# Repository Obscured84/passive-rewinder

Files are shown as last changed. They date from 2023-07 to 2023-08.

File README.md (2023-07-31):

# passive-rewinder
Files in origin_design directory are the untouched files from the creator lenglengda
Passive MMU Rewinder 

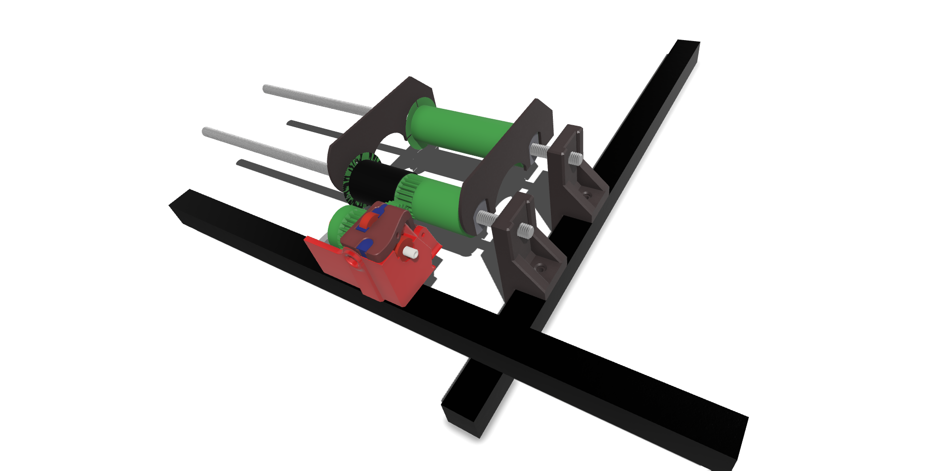
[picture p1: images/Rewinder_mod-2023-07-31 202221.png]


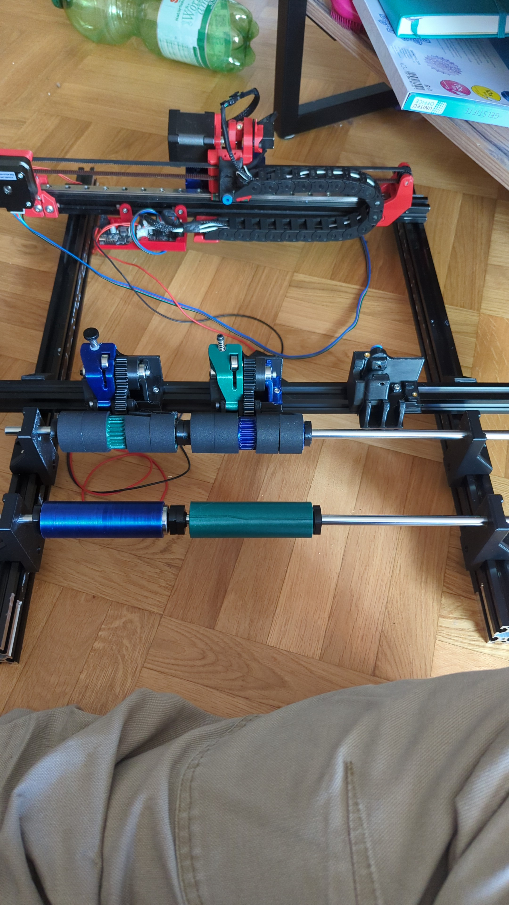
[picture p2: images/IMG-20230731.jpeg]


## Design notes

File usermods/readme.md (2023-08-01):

in case of modifications, please put them in here with your name and proper description

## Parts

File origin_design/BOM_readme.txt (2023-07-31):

BOM:
CSK8PP Clutch Bearing x1
ECAS04 x1
608 Bearing x4
625 Bearing x1
605 Bearing x3
Heat insert M3x4x5 x2
Spring 1x6x10 x1
MK8 or BMG Gear x1
M3 Washer x2
M3x6(8) x1
M3x(10+) x1
M3x(32+) x2 
M3x(48+) x1
M5x(5+) x4 (FH, Optional)
5x50 D-Shaft x1 (Optional)

Notice:
 
- Do confirm the direction of the cltuch bearing before pressing it in.
- Pad a pulley under the bearing and punch it out if it was pressed in the oppsite way.

- A SH M3x48 screw should be insert into the BMG/MK8 gear as shaft
from the side of CSK8PP. (For M3x48 screw + printed shaft user. No need if using D-shaft)
- (D-shaft is recommended for a smoother rotation)

- Install washer to both ends of the spring.
- The spring should be precompressed to keep filament from slipping.

- This rewinder is designed for 5.8L dry box.

- Install TPU sleeves to the rewinding wheel if it is too slippy.

Change Log:

1.0: First test completed
1.1: Added TPU sleeve (optional)
1.2: Adapted clutch bearing shaft to BMG and MK8 gears. Add MK8 spacer.
1.3: Fixed cracking problem of the base by adding more thickness.
1.4: Fixed pressure lever overhang issue
1.5: Change clutch bearing shaft to tightening assembly for better concentricty.
     Added drilling jig for 5.8L dry box.
1.6: Added D-shaft (optional) for better concentricty.
     Added buckle to the desiccant cap to prevent spilling out.
1.7: Fixed holes for D-shaft.
1.8: Added TPU seal for filament outlet.
2.0: Fixed filament stucking issue.
     Adjusted the hight of the lever for smoother filament change.
2.1:  Fixed the bearing seat mismatch issue.

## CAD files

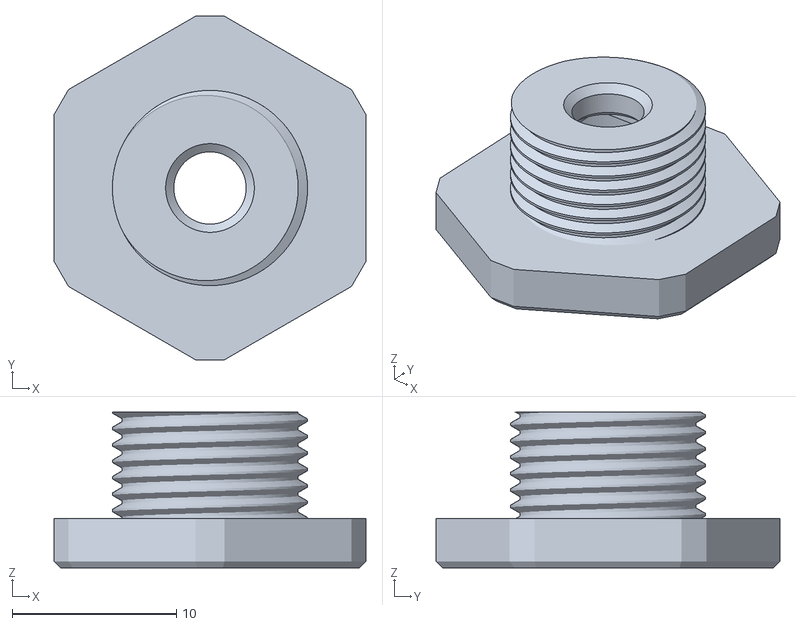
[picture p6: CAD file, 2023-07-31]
origin_design/ECAS_adapter.stl
19.0 x 20.9 x 9.50

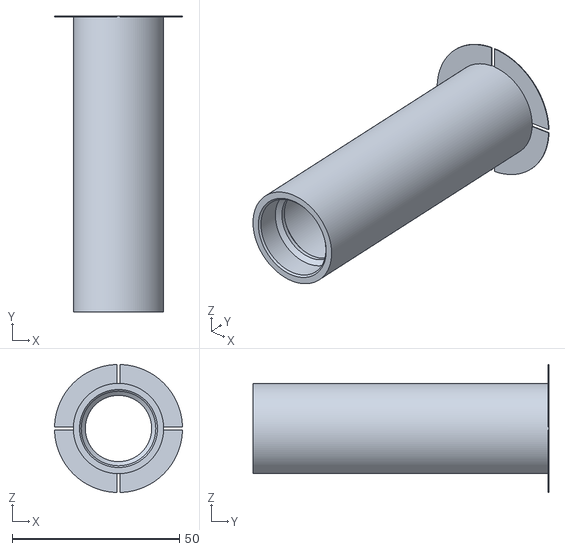
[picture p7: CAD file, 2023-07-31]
STL/Rewinder_mod_rear_spool.stl
38.3 x 88.4 x 38.3

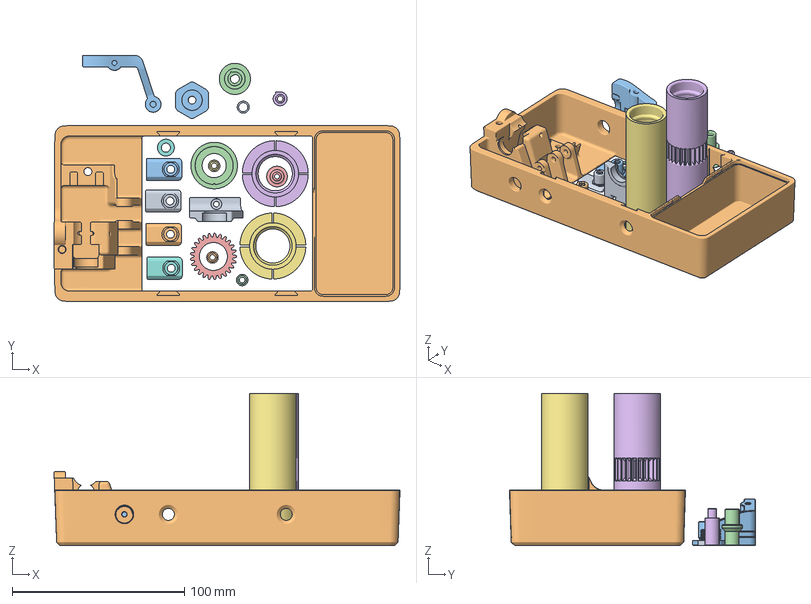
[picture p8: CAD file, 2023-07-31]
origin_design/rewinder.3mf
200.8 x 142.8 x 88.4 mm
bearing_seat.stl
base.stl
lever.stl
clutch_bearing_shaft_d_shaft.stl
clutch_bearing_shaft_screw_1.stl
clutch_bearing_shaft_screw_2.stl
605_pin.stl
605_spacer.stl
BMG_spacer.stl
625_pinx2.stl x 2
ECAS_adapter.stl
clutch_bearing_gear.stl
countershaft_gear.stl
drive_wheel.stl
driven_wheel.stl
608_pinx4.stl x 4

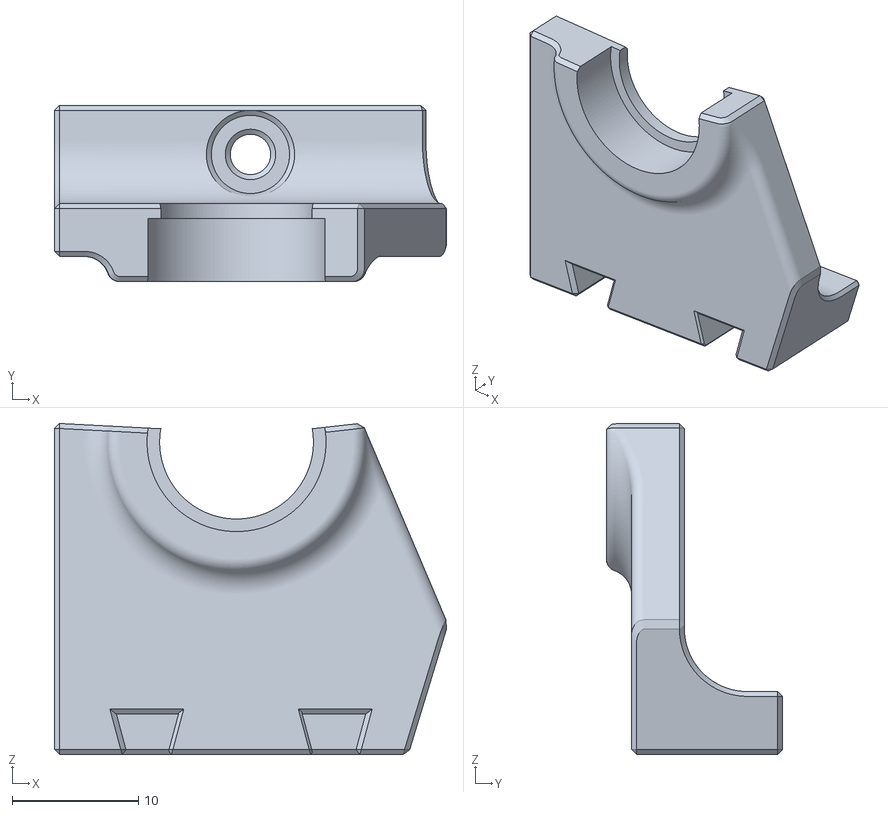
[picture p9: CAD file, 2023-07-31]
STL/Rewinder_mod_bearring_slider.stl
31.1 x 14.0 x 26.3

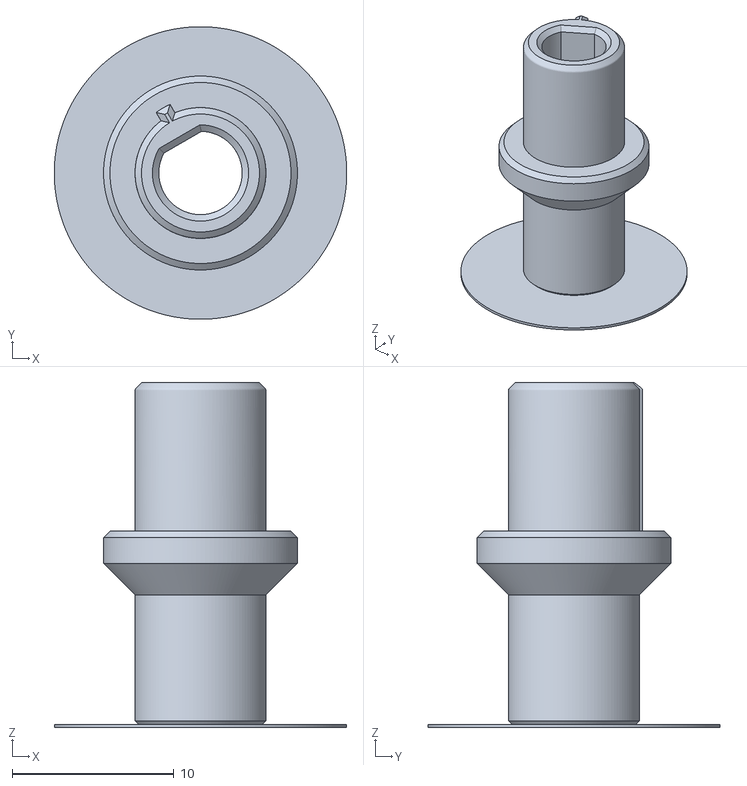
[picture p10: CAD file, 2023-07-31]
origin_design/clutch_bearing_shaft_d_shaft.stl
18.1 x 18.1 x 21.4

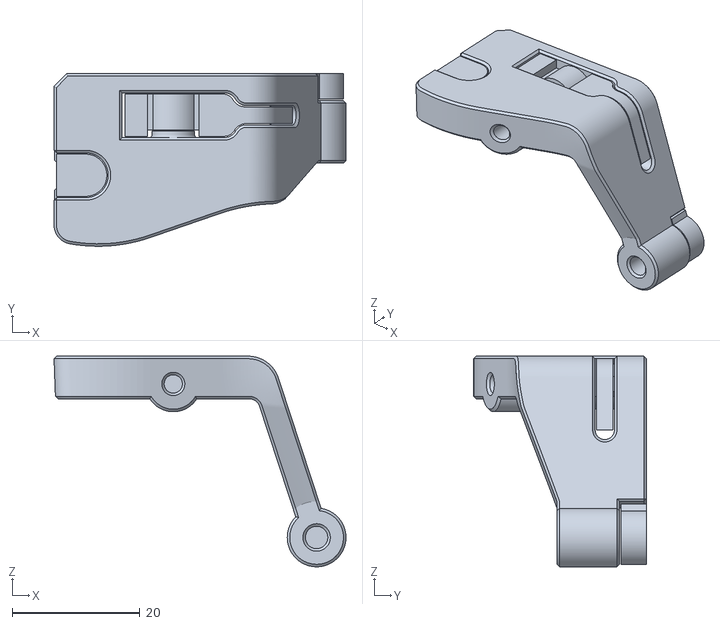
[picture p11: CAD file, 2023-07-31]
STL/Rewinder_mod_lever.stl
45.7 x 27.0 x 33.0

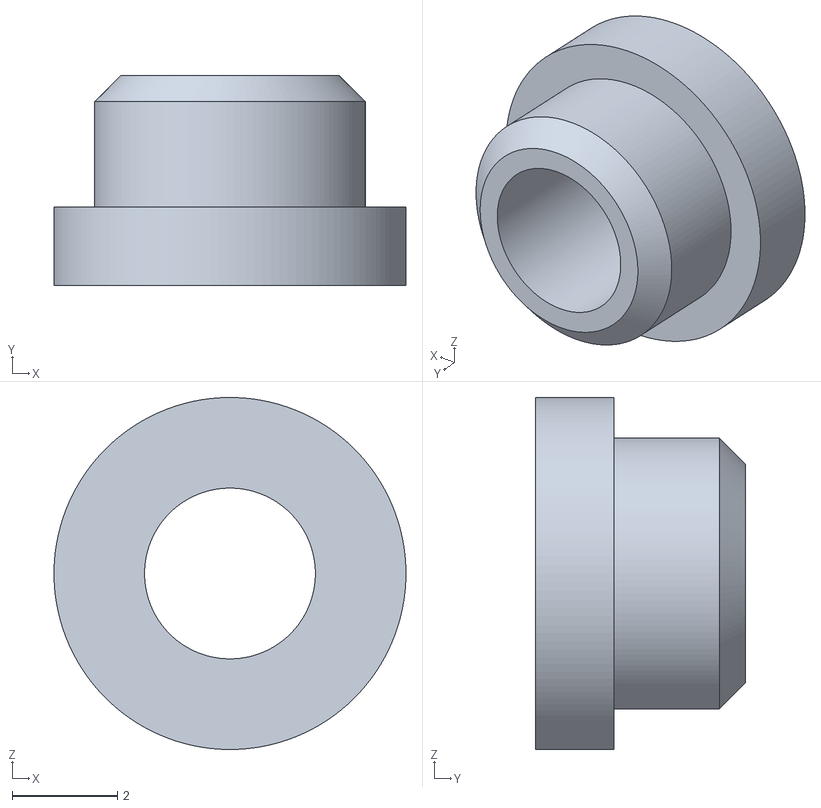
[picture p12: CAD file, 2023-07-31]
STL/Rewinder_mod_625_spacer.stl
6.70 x 4.00 x 6.70

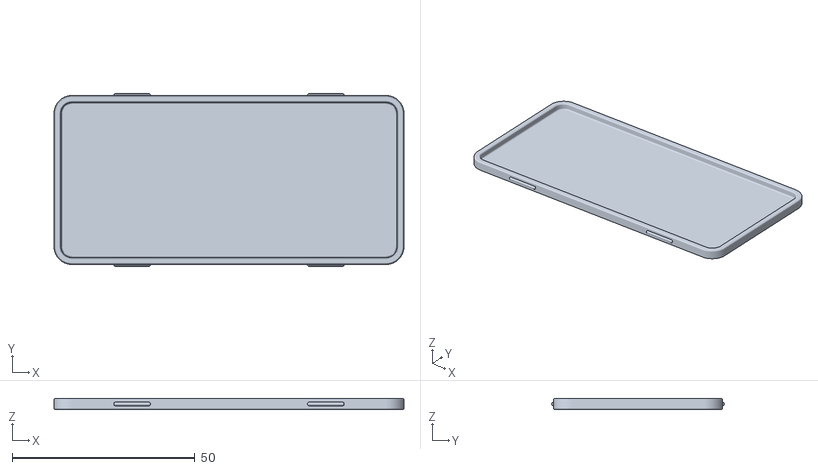
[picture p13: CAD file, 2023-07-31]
origin_design/cap.stl
95.8 x 47.2 x 3.00

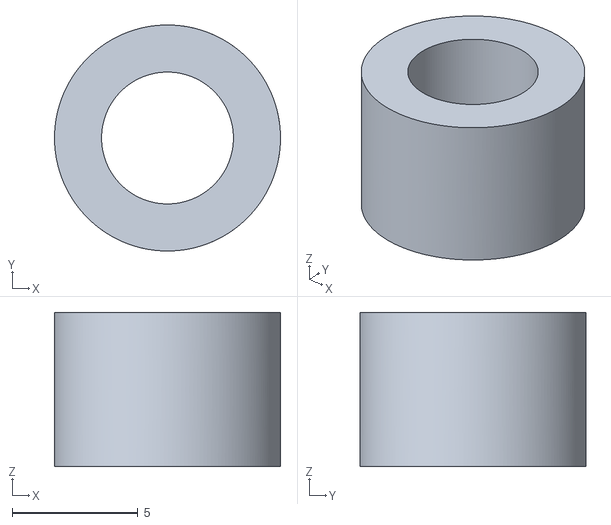
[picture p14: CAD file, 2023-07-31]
origin_design/MK8_spacer.stl
9.00 x 9.00 x 6.15

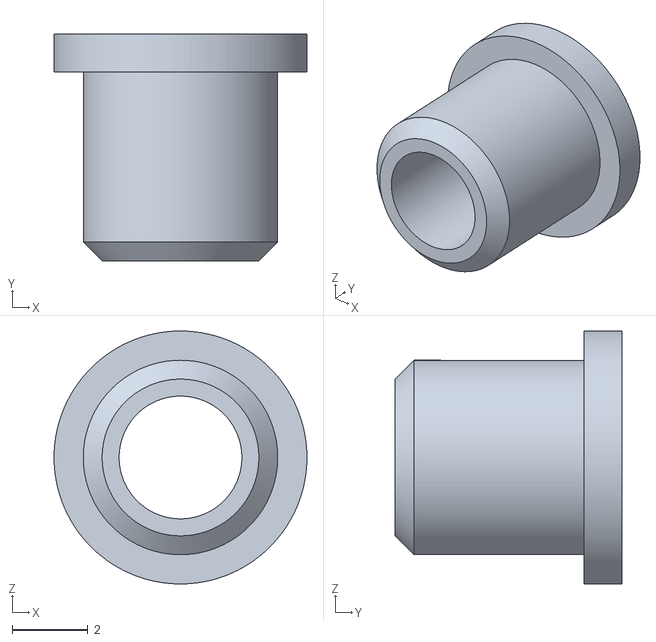
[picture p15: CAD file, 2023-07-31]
STL/Rewinder_mod_605_spacer.stl
6.70 x 6.00 x 6.70

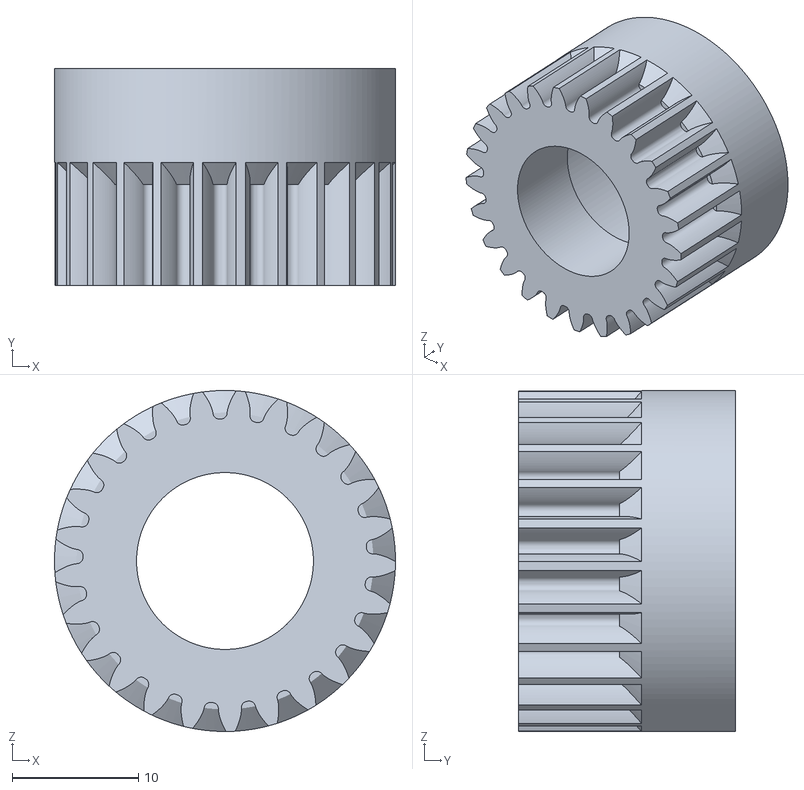
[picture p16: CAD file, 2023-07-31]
STL/Rewinder_mod_clutch_gear.stl
27.0 x 17.2 x 27.0

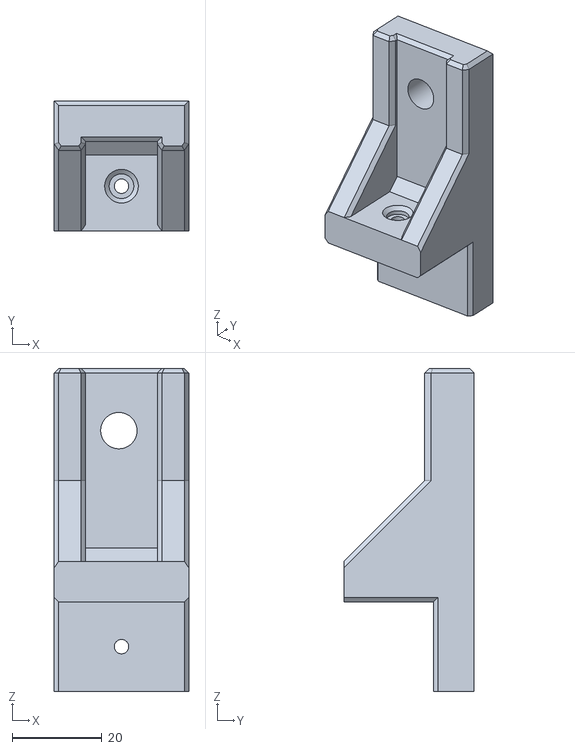
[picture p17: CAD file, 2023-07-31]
STL/Rewinder_mod_spool_anchor4x.stl
30.0 x 29.0 x 72.0

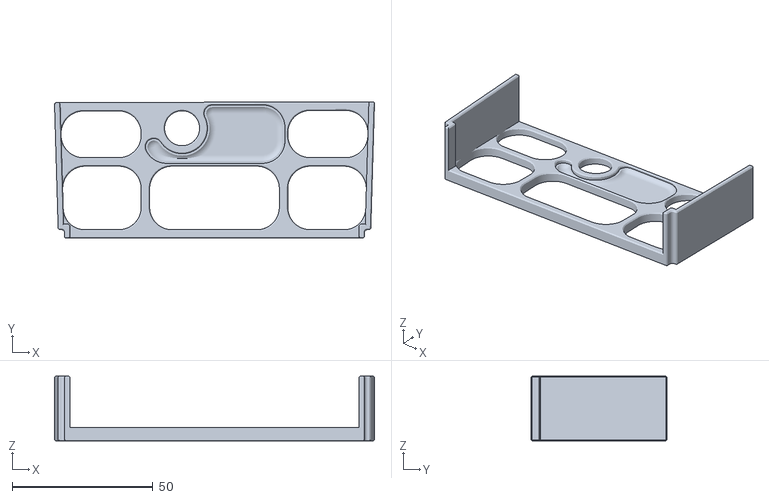
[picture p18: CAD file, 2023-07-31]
origin_design/drilling_jig.stl
113.5 x 48.4 x 23.0

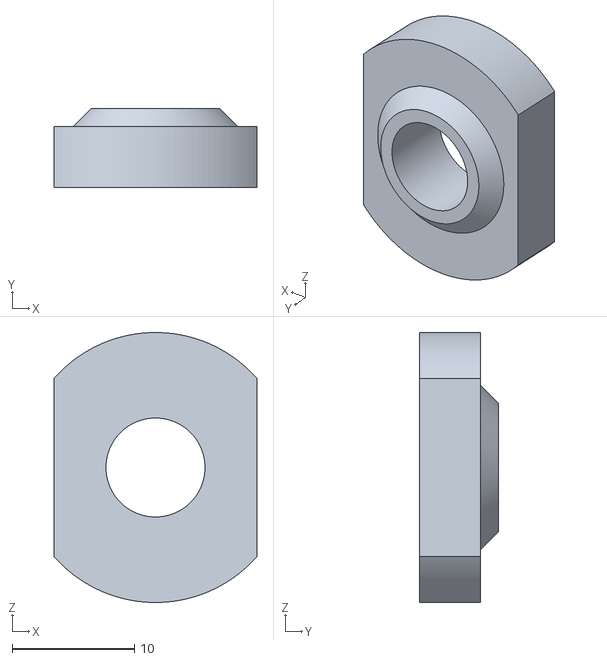
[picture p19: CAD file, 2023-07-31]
STL/Rewinder_mod_608_spacer4x.stl
16.6 x 6.50 x 22.1

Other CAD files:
STL/Rewinder_mod_clutch_d-shaft.stl
origin_design/driven_wheel.stl
origin_design/625_pinx2.stl
origin_design/clutch_bearing_gear.stl
STL/Rewinder_mod_605_washer.stl
STL/Rewinder_mod_BMG_spacer.stl
STL/Rewinder_mod_TPU_spool-sleeve.stl
STL/Rewinder_mod_clutch_part_a.stl
STL/Rewinder_mod_clutch_part_b.stl
STL/Rewinder_mod_front_spool.stl
STL/Rewinder_mod_mid_gear.stl
STL/Rewinder_mod_separator2x.stl
origin_design/605_pin.stl
origin_design/605_spacer.stl
origin_design/608_pinx4.stl
origin_design/BMG_spacer.stl
origin_design/TPU_seal.stl
origin_design/TPU_sleevex2.stl
origin_design/bearing_seat.stl
origin_design/clutch_bearing_shaft_screw_1.stl
origin_design/clutch_bearing_shaft_screw_2.stl
origin_design/countershaft_gear.stl
origin_design/drive_wheel.stl
origin_design/lever.stl
